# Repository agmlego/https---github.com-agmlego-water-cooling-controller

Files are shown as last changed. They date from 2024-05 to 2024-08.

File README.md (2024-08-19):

External Water-Cooling Loop Controller
--------------------------------------

The intent of this project is to monitor and control an external chiller system for a PC water-cooling loop with a liquid-liquid heat exchanger to separate the internal and external loops.

There is a PCIe x1 card inside the PC, tapping into SMBus and +3V3AUX, to monitor the flow, inlet, and outlet temperatures for the internal and external loops, and intercept the front panel power switch to prevent boot or to initiate a shutdown if the loops are not working correctly. The Teensy 3.2 will communicate to the PC, pretending to be a common SMBus device such as those from Winbond or Nuvoton. It also talks with an external board in the chiller over RS232. Onboard WS2811B and an OLED screen show immediate diagnostics. An onboard BME280 lets the Teensy monitor internal case ambient temperature and humidity, to ensure that the chiller does not drop below the local dewpoint to prevent condensation.

The external board listens to RS232 and adjusts the chiller's power state and setpoint. It also reports the local BME280 results and has an onboard OLED screen for system status.

## Internal PCIe Card

| Pin | Type | Signal | Direction | Purpose |
| --- | --- | --- | --- | --- |
| 1 | POWER | GND | | Digital ground plane |
| 2 | DIGITAL | D0 | INPUT | Internal loop flow sensor |
| 3 | DIGITAL | D1 | INPUT | External loop flow sensor |
| 7 | DIGITAL | D5 | OUTPUT | Level shifter output enable, active low |
| 8 | DIGITAL | D6 | INPUT | PCIe #PERST status |
| 9 | DIGITAL | D7 | OUTPUT | WS2811B data |
| 11  | RS232 | RX | INPUT | RS232 receive |
| 12  | RS232 | TX | OUTPUT | RS232 transmit |
| 21  | ANALOG  | A0 | INPUT | External loop outflow temperature, 10k NTC |
| 22  | ANALOG  | A1 | INPUT | External loop inflow temperature, 10k NTC |
| 23  | ANALOG  | A2 | INPUT | Internal loop inflow temperature, 10k NTC  |
| 24  | ANALOG  | A3 | INPUT | Internal loop outflow temperature, 10k NTC |
| 25  | I2C | SDA0 | BIDI | SMBus I2C data |
| 26  | I2C | SCL0 | BIDI | SMBus I2C clock |
| 29  | DIGITAL | D22 | OUTPUT | Front panel power switch output |
| 30  | DIGITAL | D23 | INPUT | Front panel power switch input |
| 31  | POWER | 3V3 | | 3.3V AUX input |
| 32  | POWER | AGND | | Analog ground plane |
| 42  | POWER | 3V3 | | 3.3V AUX input |
| 46  | I2C | SDA1 | BIDI | Local I2C data |
| 47  | I2C | SCL1 | BIDI | Local I2C clock |
| 53  | POWER | GND | | Digital ground plane |

### WS2811B

1. External loop temperature status
2. External loop flow status
3. Internal loop temperature status
4. Internal loop flow status

### RS232 DE-9

0. Chassis earth
1. N/C
2. PC RX
3. PC TX
4. N/C
5. 0VDC
6. N/C
7. N/C
8. N/C
9. +5V

### Images
top
bottom
[Interactive BOM](https://agmlego.github.io/water-cooling-controller/pcie/ibom.html)

## Chiller Controller

| Pin | Type | Signal | Direction | Purpose |
| --- | --- | --- | --- | --- |
| 1 | POWER | GND | | Digital ground |
| 2 | RS232 | RX | INPUT | RS232 receive |
| 3 | RS232 | TX | OUTPUT | RS232 transmit |
| 4 | 1-WIRE  | D2 | BIDI | DS18B20 bus |
| 10  | DIGITAL | D8 | OUTPUT | Expansion valve relay |
| 11  | DIGITAL | D9 | OUTPUT | Compressor relay |
| 12  | DIGITAL | D10 | OUTPUT | [Fan PWM](#nf-a14-control) |
| 13  | DIGITAL | D11 | INPUT | Bottom fan RPM sensor |
| 14  | DIGITAL | D12 | INPUT | Top fan RPM sensor |
| 20  | DIGITAL | D13 | OUTPUT | Status lights/buzzer relay |
| 21  | DIGITAL | D14 | OUTPUT | Pump relay |
| 22  | DIGITAL | D15 | INPUT | Flow switch, active low |
| 23  | I2C | SCL0 | BIDI | Local I2C clock |
| 24  | I2C | SDA0 | BIDI | Local I2C data |
| 25  | DIGITAL | D18 | INPUT | Encoder switch |
| 26  | DIGITAL | D19 | INPUT | Encoder quadrature B |
| 27  | DIGITAL | D20 | INPUT | Encoder quadrature A |
| 28  | ANALOG  | A7 | INPUT | Filter check diff. pressure sensor |
| 29  | ANALOG  | A8 | INPUT | Reservoir eTape R<sub>ref</sub> 2000Ω |
| 30  | ANALOG  | A9 | INPUT | Reservoir eTape R<sub>sense</sub> 400-2000Ω |
| 31  | POWER | 3V3 | | 3.3V output |
| 32  | POWER | AGND | | Analog ground |
| 33  | POWER | 5V | | 5V input from CAN |

### JST-XH Connectors

#### RS232
| Pin | Type  | Signal | Direction | Purpose |
| --- | ----- | --- | --- | --- |
| 1 | POWER | 5V | | 5V from PCIe card |
| 2 | POWER | GND | | Digital ground |
| 3 | RS232 | RX | INPUT | RS232 receive |
| 4 | RS232 | TX | OUTPUT | RS232 transmit |

#### Flow
| Pin | Type | Signal | Direction | Purpose |
| --- | --- | --- | --- | --- |
| 1 | DIGITAL | D15 | INPUT | Flow switch |
| 2 | POWER | GND | | Digital ground |

#### DS18B20 One-Wire
| Pin | Type | Signal | Direction | Purpose |
| --- | --- | --- | --- | --- |
| 1 | 1-WIRE | D2 | BIDI | DS18B20 bus |
| 2 | POWER  | GND | | Digital ground |
| 3 | POWER  | 3V3 | | 3.3V output |

#### Filter Diff. Pressure
| Pin | Type | Signal | Direction | Purpose |
| --- | --- | --- | --- | --- |
| 1 | POWER  | 3V3 | | 3.3V output |
| 2 | POWER  | AGND | | Analog ground |
| 3 | ANALOG | A7 | INPUT | Filter check diff. pressure sensor |

#### Reservoir Level eTape
| Pin | Type | Signal | Direction | Purpose |
| --- | --- | --- | --- | --- |
| 1 | ANALOG | A9 | INPUT | R<sub>sense</sub> 400-2000Ω |
| 2 | ANALOG | A8 | INPUT | R<sub>ref</sub> 2000Ω |
| 3 | POWER  | AGND | | Analog ground |
| 4 | POWER  | AGND | | Analog ground |

#### Fans
| Pin | Type | Signal | Direction | Purpose |
| --- | --- | --- | --- | --- |
| 1 | DIGITAL | D12 | INPUT | Top fan RPM sensor |
| 2 | DIGITAL | D11 | INPUT | Bottom fan RPM sensor |
| 3 | DIGITAL | D10 | OUTPUT | Fan PWM |

#### Dual-Relay Module
| Pin | Type | Signal | Direction | Purpose |
| --- | --- | --- | --- | --- |
| 1 | POWER | GND | | Digital ground |
| 2 | DIGITAL | D13 | OUTPUT | Status lights/buzzer relay |
| 3 | DIGITAL | D14 | OUTPUT | Pump relay |
| 4 | POWER | 5V | | 5V input from CAN |

#### SSRs
| Pin | Type | Signal | Direction | Purpose |
| --- | --- | --- | --- | --- |
| 1 | POWER | GND | | Digital ground |
| 2 | DIGITAL | D9 | OUTPUT | Compressor relay |
| 3 | POWER | GND | | Digital ground |
| 4 | DIGITAL | D8 | OUTPUT | Expansion valve relay |

### NF-A14 Control
* PWM: 40μs period, 5Vpp
* 8.76% minimum kickon => 468RPM (64ms/15.6Hz on tach.)
* 100% => 3180RPM (9.4ms/106.4Hz on tach.)

### Images
top
bottom
[Interactive BOM](https://agmlego.github.io/water-cooling-controller/cw5200/ibom.html)

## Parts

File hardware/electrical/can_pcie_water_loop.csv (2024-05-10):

Source: | D:\documents\projects\home_automation\can_pcie_water_loop\can_pcie_water_loop.kicad_sch
Date: | 2023-08-21 20:34:38
Tool: | Eeschema (7.0.0)
Generator: | C:\Program Files\KiCad\7.0\bin\scripting\plugins/bom_csv_grouped_by_value_with_fp.py
Component Count: | 56
Ref | Qnty | Value | Cmp name | Footprint | Description | Vendor | DNP
C1 | 1 | 4700pF | C_Small | Capacitor_SMD:C_1206_3216Metric | Unpolarized capacitor, small symbol
C2, C3 | 2 | 0.1uF | C_Small | Capacitor_SMD:C_1206_3216Metric | Unpolarized capacitor, small symbol
D1, D2, D3, D4, D5, D6 | 6 | GREEN | LED_Small | LED_SMD:LED_1206_3216Metric | Light emitting diode, small symbol
D7 | 1 | Ext T Stat | WS2812B | LED_SMD:LED_WS2812B_PLCC4_5.0x5.0mm_P3.2mm | RGB LED with integrated controller
D8 | 1 | Ext Flo Stat | WS2812B | LED_SMD:LED_WS2812B_PLCC4_5.0x5.0mm_P3.2mm | RGB LED with integrated controller
D9 | 1 | Int T Stat | WS2812B | LED_SMD:LED_WS2812B_PLCC4_5.0x5.0mm_P3.2mm | RGB LED with integrated controller
D10 | 1 | Int Flo Stat | WS2812B | LED_SMD:LED_WS2812B_PLCC4_5.0x5.0mm_P3.2mm | RGB LED with integrated controller
H1, H2 | 2 | PCIe Bracket | MountingHole_Pad | MountingHole:MountingHole_3.2mm_M3_Pad_Via | Mounting Hole with connection
H3, H4, H5, H6 | 4 | OLED | MountingHole | MountingHole:MountingHole_2.2mm_M2 | Mounting Hole without connection
H7 | 1 | BME280 | MountingHole | MountingHole:MountingHole_3.2mm_M3 | Mounting Hole without connection
J1 | 1 | Bus_PCI_Express_x1 | Bus_PCI_Express_x1 | Connector_PCBEdge:BUS_PCIexpress_x1 | PCI Express bus connector x1
J2 | 1 | CAN | DE9_Plug_MountingHoles | Connector_Dsub:DSUB-9_Female_Horizontal_P2.77x2.84mm_EdgePinOffset7.70mm_Housed_MountingHolesOffset9.12mm | 9-pin male plug pin D-SUB connector, Mounting Hole
J3 | 1 | Int T Hi | Conn_01x02_Pin | Connector_PinHeader_2.54mm:PinHeader_1x02_P2.54mm_Horizontal | Generic connector, single row, 01x02, script generated
J4 | 1 | Int T Lo | Conn_01x02_Pin | Connector_PinHeader_2.54mm:PinHeader_1x02_P2.54mm_Horizontal | Generic connector, single row, 01x02, script generated
J5 | 1 | Ext T Hi | Conn_01x02_Pin | Connector_PinHeader_2.54mm:PinHeader_1x02_P2.54mm_Horizontal | Generic connector, single row, 01x02, script generated
J6 | 1 | Ext T Lo | Conn_01x02_Pin | Connector_PinHeader_2.54mm:PinHeader_1x02_P2.54mm_Horizontal | Generic connector, single row, 01x02, script generated
J7 | 1 | BME280 I2C | Conn_01x04_Pin | Connector_PinHeader_2.54mm:PinHeader_1x04_P2.54mm_Vertical | Generic connector, single row, 01x04, script generated
J8 | 1 | Disp I2C | Conn_01x04_Pin | Connector_PinHeader_2.54mm:PinHeader_1x04_P2.54mm_Vertical | Generic connector, single row, 01x04, script generated
J9 | 1 | Int Flo | Conn_01x03_Pin | Connector_PinHeader_2.54mm:PinHeader_1x03_P2.54mm_Horizontal | Generic connector, single row, 01x03, script generated
J10 | 1 | Ext Flo | Conn_01x03_Pin | Connector_PinHeader_2.54mm:PinHeader_1x03_P2.54mm_Horizontal | Generic connector, single row, 01x03, script generated
J11 | 1 | SW In | Conn_01x02_Pin | Connector_PinHeader_2.54mm:PinHeader_1x02_P2.54mm_Horizontal | Generic connector, single row, 01x02, script generated
J12 | 1 | SW Out | Conn_01x02_Pin | Connector_PinHeader_2.54mm:PinHeader_1x02_P2.54mm_Horizontal | Generic connector, single row, 01x02, script generated
J13 | 1 | SMBus | Conn_01x04_Pin | Connector_PinHeader_2.54mm:PinHeader_1x04_P2.54mm_Vertical | Generic connector, single row, 01x04, script generated
R1, R7, R8, R17, R18 | 5 | 10k | R_Small_US | Resistor_SMD:R_1206_3216Metric | Resistor, small US symbol
R2 | 1 | 200 | R_Small_US | Resistor_SMD:R_1206_3216Metric | Resistor, small US symbol
R3, R4, R5, R6 | 4 | 100k | R_Small_US | Resistor_SMD:R_1206_3216Metric | Resistor, small US symbol
R9, R10 | 2 | 60 | R_Small_US | Resistor_SMD:R_1206_3216Metric | Resistor, small US symbol
R11 | 1 | 300 | R_Small_US | Resistor_SMD:R_1206_3216Metric | Resistor, small US symbol
R12, R13, R14, R15, R16 | 5 | 220 | R_Small_US | Resistor_SMD:R_1206_3216Metric | Resistor, small US symbol
U1 | 1 | Teensy3.2 | Teensy3.2 | teensy:Teensy30_31_32_All_Pins
U2 | 1 | MCP2561 | MCP2561-E-SN | Package_SO:SOIC-8_3.9x4.9mm_P1.27mm | High-Speed CAN Transceiver, 1Mbps, 5V supply, SPLIT pin, -40C to +125C, SOIC-8
U3 | 1 | CNY17-3 | CNY17-3 | Package_DIP:SMDIP-6_W7.62mm | DC Optocoupler Base Connected, Vce 70V, CTR 100-200%, Viso 5000V (RMS), DIP6
U4 | 1 | Pololu U3V16F5 | TSR_1-2412 | Connector_PinHeader_2.54mm:PinHeader_1x03_P2.54mm_Vertical | 1A step-down regulator module, fixed 1.2V output voltage, 6-36V input voltage, -40°C to +85°C temperature range, TO-220 compatible LM78xx replacement
U5 | 1 | 74125 | SN74LV4T125 | Package_SO:TSSOP-14_4.4x5mm_P0.65mm | Single Supply Logic Level Translator Quad Buffer with 3-State Outputs

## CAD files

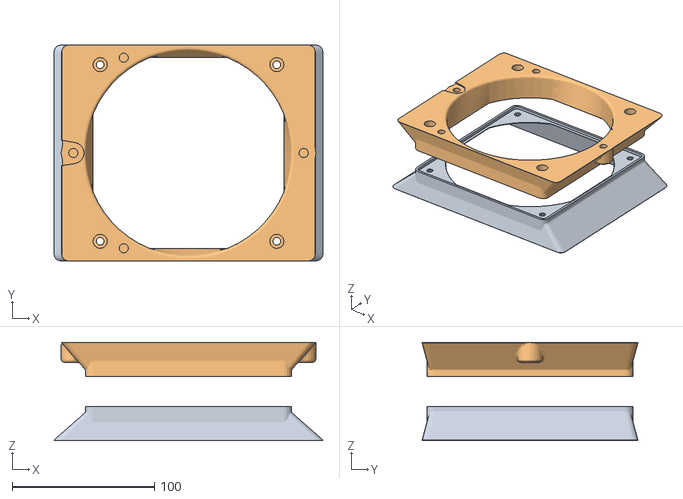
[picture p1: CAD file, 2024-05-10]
hardware/mechanical/nf-a14_ducting.obj
189.2 x 151.8 x 69.0
coil_side
exhaust_side

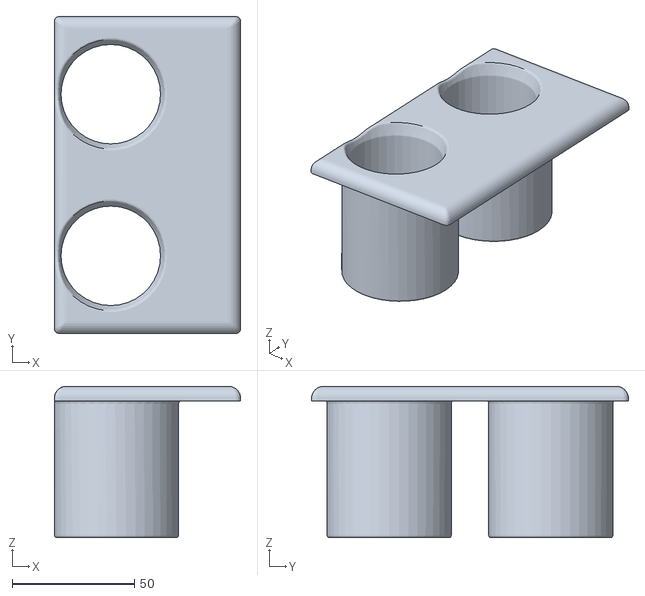
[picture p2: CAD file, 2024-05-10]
hardware/mechanical/wall_passthrough.obj
76.2 x 129.5 x 61.9

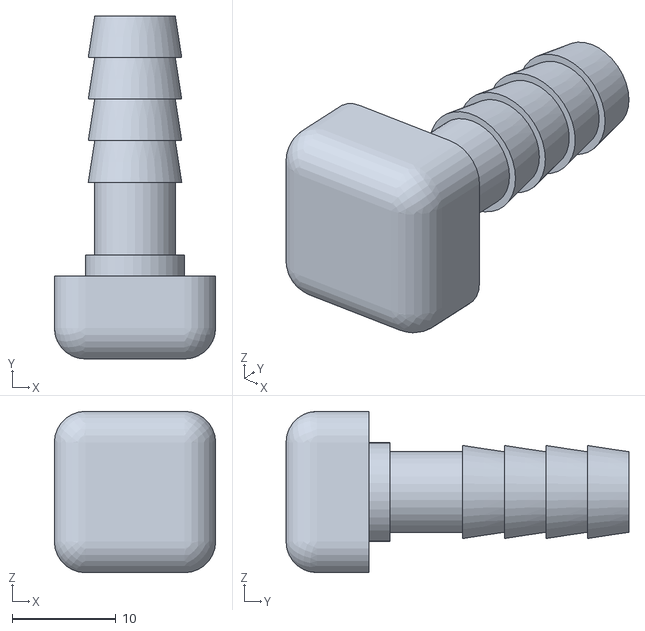
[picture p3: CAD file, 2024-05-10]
hardware/mechanical/vacuum_vent.obj
15.5 x 33.0 x 15.5

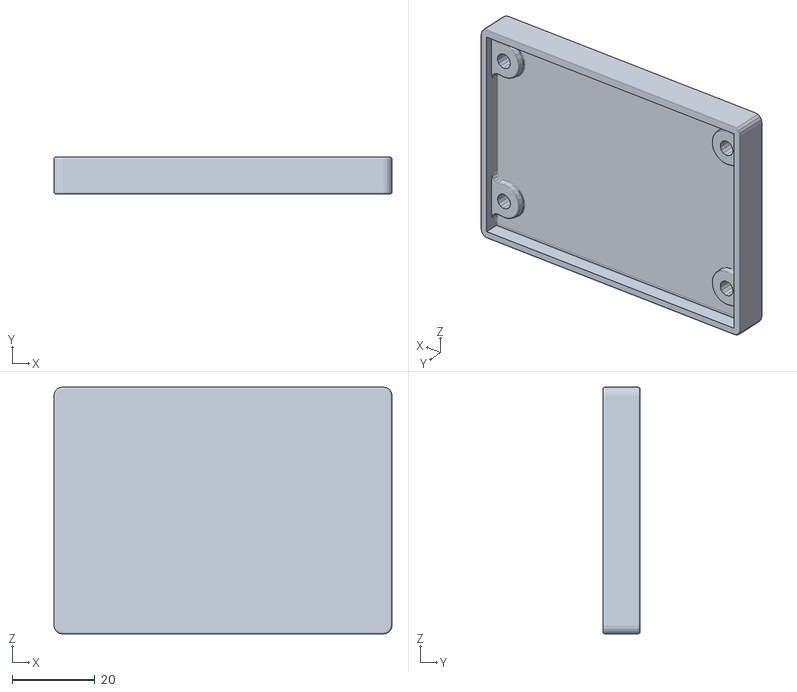
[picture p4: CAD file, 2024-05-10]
hardware/mechanical/vma400_isolator.obj
81.5 x 9.00 x 59.5

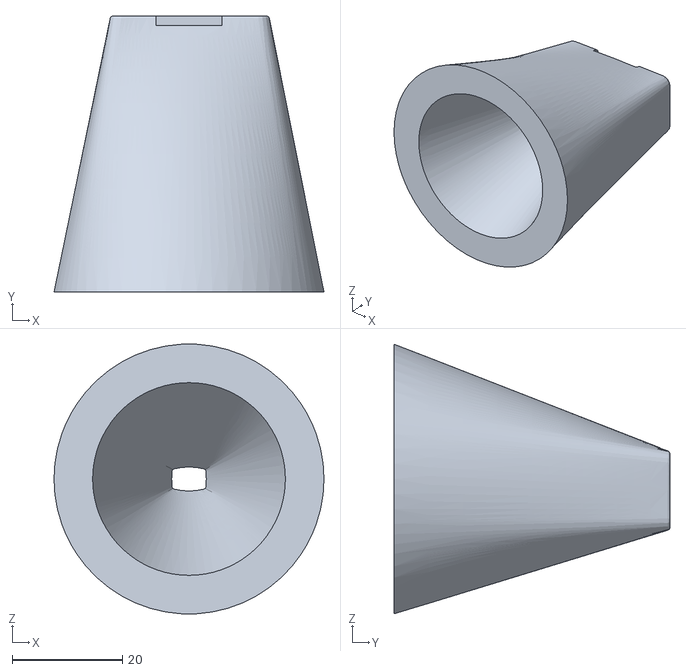
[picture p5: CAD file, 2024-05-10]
hardware/mechanical/VL53L0X_standoff.obj
48.9 x 50.0 x 48.8

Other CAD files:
hardware/mechanical/VL53L0X_standoff.ipt
hardware/mechanical/nf-a14.ipt
hardware/mechanical/nf-a14_ducting.ipt
hardware/mechanical/vacuum_vent.ipt
hardware/mechanical/vma400_isolator.ipt
hardware/mechanical/wall_passthrough.ipt

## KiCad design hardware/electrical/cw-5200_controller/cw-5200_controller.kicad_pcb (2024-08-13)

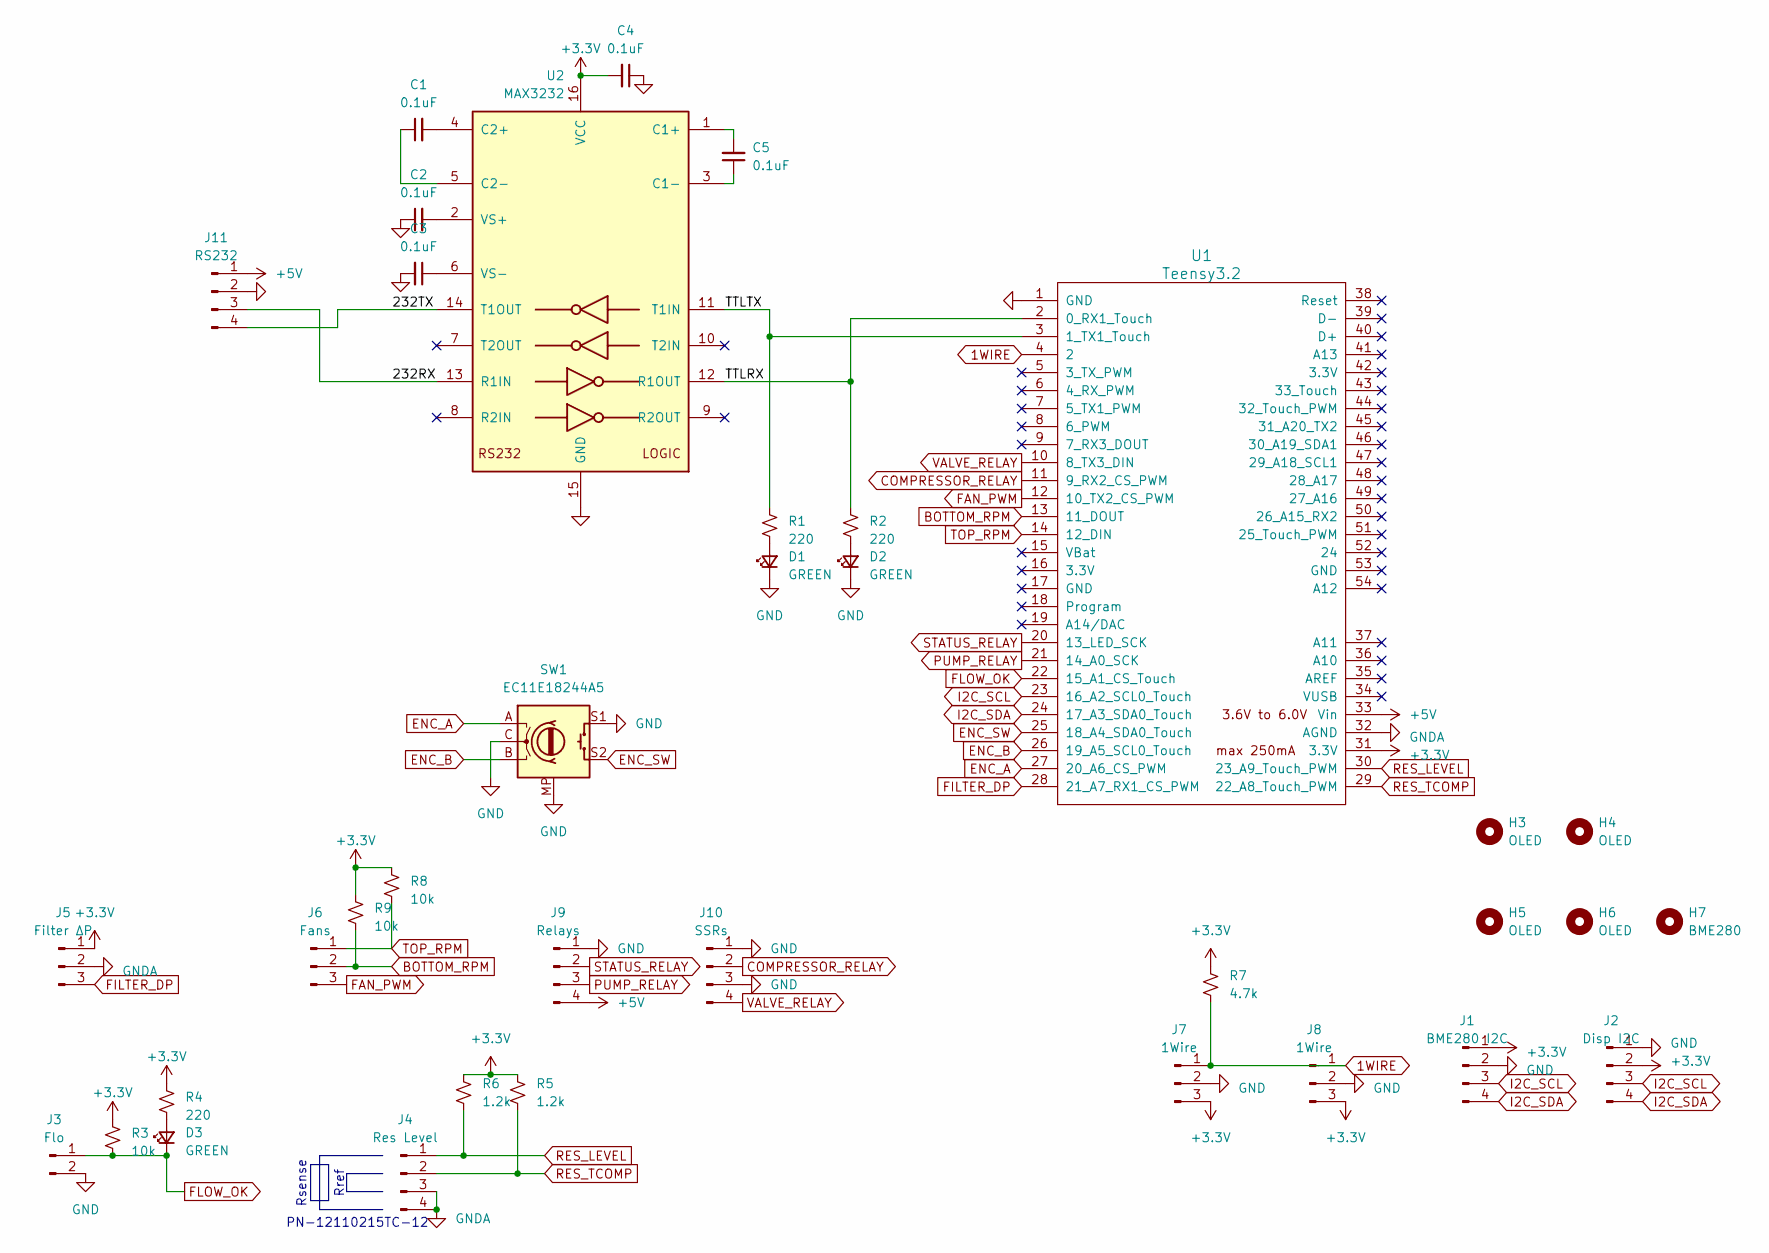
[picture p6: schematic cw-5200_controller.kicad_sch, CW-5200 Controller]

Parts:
C1, C2, C3, C4, C5: 0.1uF; C_1206_3216Metric
D1, D2, D3: GREEN; LED_1206_3216Metric
H3, H4, H5, H6: OLED; MountingHole_2.2mm_M2
H7: BME280; MountingHole_3.2mm_M3
J1: BME280 I2C; PinHeader_1x04_P2.54mm_Vertical
J2: Disp I2C; PinHeader_1x04_P2.54mm_Vertical
J3: Flo; JST_XH_B2B-XH-A_1x02_P2.50mm_Vertical
J4: Res Level; JST_XH_B4B-XH-A_1x04_P2.50mm_Vertical
J5: Filter ΔP; JST_XH_B3B-XH-A_1x03_P2.50mm_Vertical
J6: Fans; JST_XH_B3B-XH-A_1x03_P2.50mm_Vertical
J7, J8: 1Wire; JST_XH_B3B-XH-A_1x03_P2.50mm_Vertical
J9: Relays; JST_XH_B4B-XH-A_1x04_P2.50mm_Vertical
J10: SSRs; JST_XH_B4B-XH-A_1x04_P2.50mm_Vertical
J11: RS232; JST_XH_B4B-XH-A_1x04_P2.50mm_Vertical
R1, R2, R4: 220; R_1206_3216Metric
R3, R8, R9: 10k; R_1206_3216Metric
R5, R6: 1.2k; R_1206_3216Metric
R7: 4.7k; R_1206_3216Metric
SW1: EC11E18244A5; RotaryEncoder_Alps_EC11E-Switch_Vertical_H20mm
U1: Teensy3.2; Teensy30_31_32_All_Pins
U2: MAX3232; TSSOP-16_4.4x5mm_P0.65mm

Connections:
1WIRE: J7.1, J8.1, R7.1, U1.4 (2)
+3.3V: C4.2, J1.1, J2.2, J5.1, J7.3, J8.3, R3.1, R4.1, R5.2, R6.1, R7.2, R8.1, R9.1, U1.31 (3.3V), U2.16 (VCC)
+5V: J9.4, J11.1, U1.33 (Vin)
/232RX: J11.3, U2.13 (R1IN)
/232TX: J11.4, U2.14 (T1OUT)
/TTLRX: R2.1, U1.2 (0_RX1_Touch), U2.12 (R1OUT)
/TTLTX: R1.1, U1.3 (1_TX1_Touch), U2.11 (T1IN)
BOTTOM_RPM: J6.2, R9.2, U1.13 (11_DOUT)
COMPRESSOR_RELAY: J10.2, U1.11 (9_RX2_CS_PWM)
ENC_A: SW1.A, U1.27 (20_A6_CS_PWM)
ENC_B: SW1.B, U1.26 (19_A5_SCL0_Touch)
ENC_SW: SW1.S2, U1.25 (18_A4_SDA0_Touch)
FAN_PWM: J6.3, U1.12 (10_TX2_CS_PWM)
FILTER_DP: J5.3, U1.28 (21_A7_RX1_CS_PWM)
FLOW_OK: D3.1 (K), J3.1, R3.2, U1.22 (15_A1_CS_Touch)
GND: C2.1, C3.2, C4.1, D1.1 (K), D2.1 (K), J1.2, J2.1, J3.2, J7.2, J8.2, J9.1, J10.1, J10.3, J11.2, SW1.C, SW1.MP, SW1.S1, U1.1 (GND), U2.15 (GND)
GNDA: J4.3, J4.4, J5.2, U1.32 (AGND)
I2C_SCL: J1.3, J2.3, U1.23 (16_A2_SCL0_Touch)
I2C_SDA: J1.4, J2.4, U1.24 (17_A3_SDA0_Touch)
unnamed: D1.2 (A), R1.2
unnamed: D2.2 (A), R2.2
unnamed: D3.2 (A), R4.2
unnamed: C5.2, U2.1 (C1+)
unnamed: C5.1, U2.3 (C1-)
unnamed: C1.2, U2.4 (C2+)
unnamed: C1.1, U2.5 (C2-)
unnamed: C2.2, U2.2 (VS+)
unnamed: C3.1, U2.6 (VS-)
PUMP_RELAY: J9.3, U1.21 (14_A0_SCK)
RES_LEVEL: J4.1, R6.2, U1.30 (23_A9_Touch_PWM)
RES_TCOMP: J4.2, R5.1, U1.29 (22_A8_Touch_PWM)
STATUS_RELAY: J9.2, U1.20 (13_LED_SCK)
TOP_RPM: J6.1, R8.2, U1.14 (12_DIN)
VALVE_RELAY: J10.4, U1.10 (8_TX3_DIN)

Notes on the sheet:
PN-12110215TC-12
Rref
Rsense

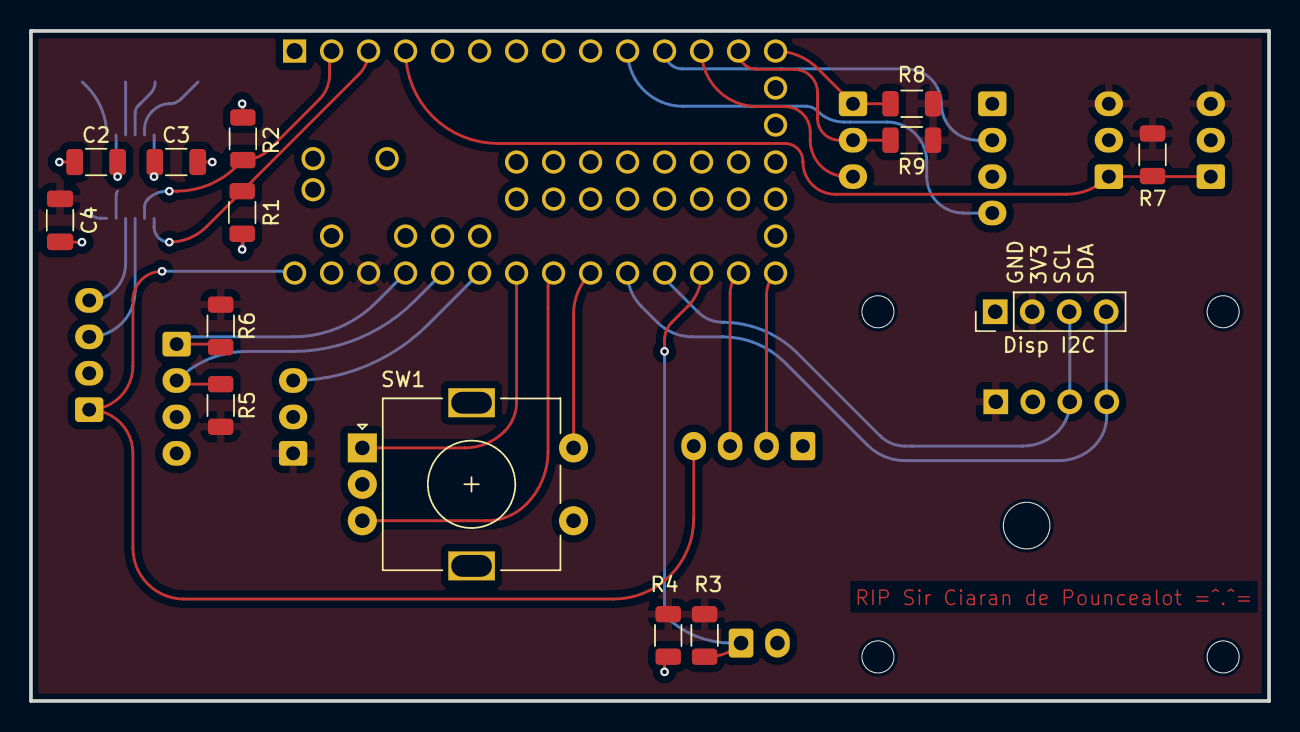
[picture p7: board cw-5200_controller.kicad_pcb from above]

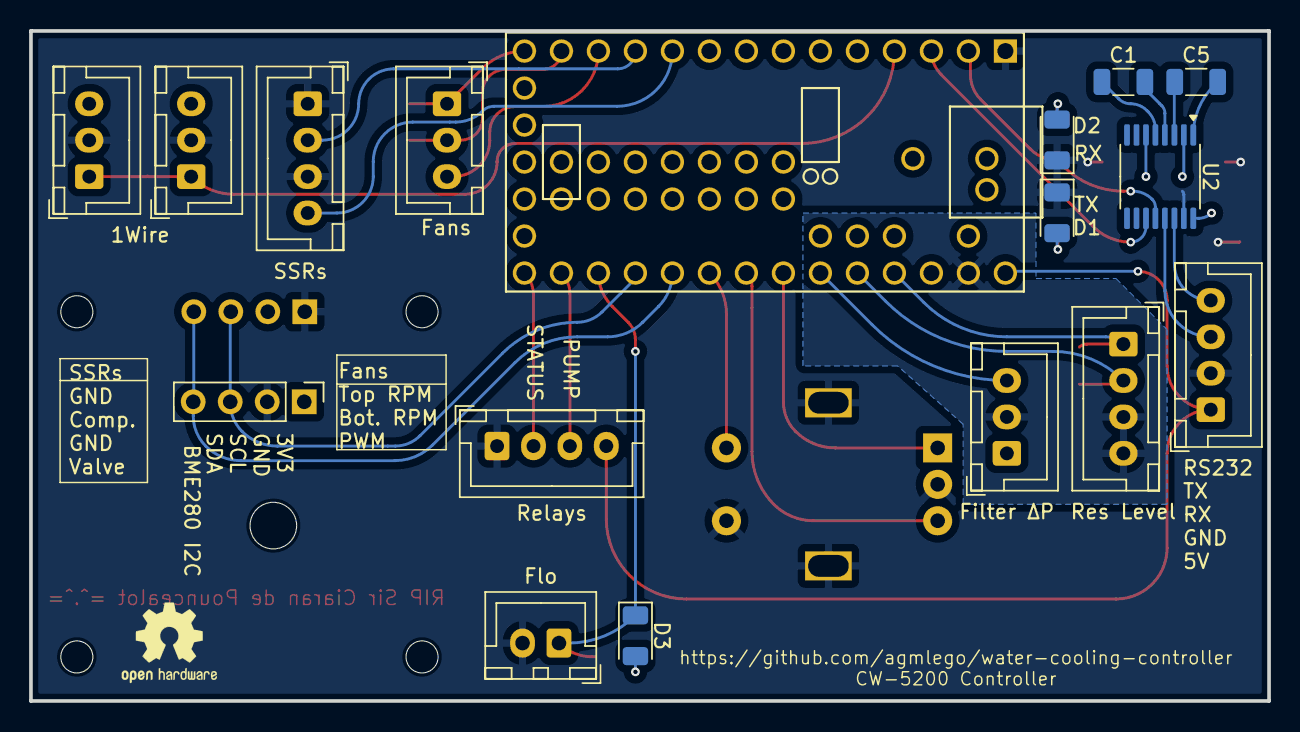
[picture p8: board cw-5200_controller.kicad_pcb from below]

Board: 2 copper layers, 85.0 x 46.0 mm, 36 parts (17 on the bottom side), 34 nets.

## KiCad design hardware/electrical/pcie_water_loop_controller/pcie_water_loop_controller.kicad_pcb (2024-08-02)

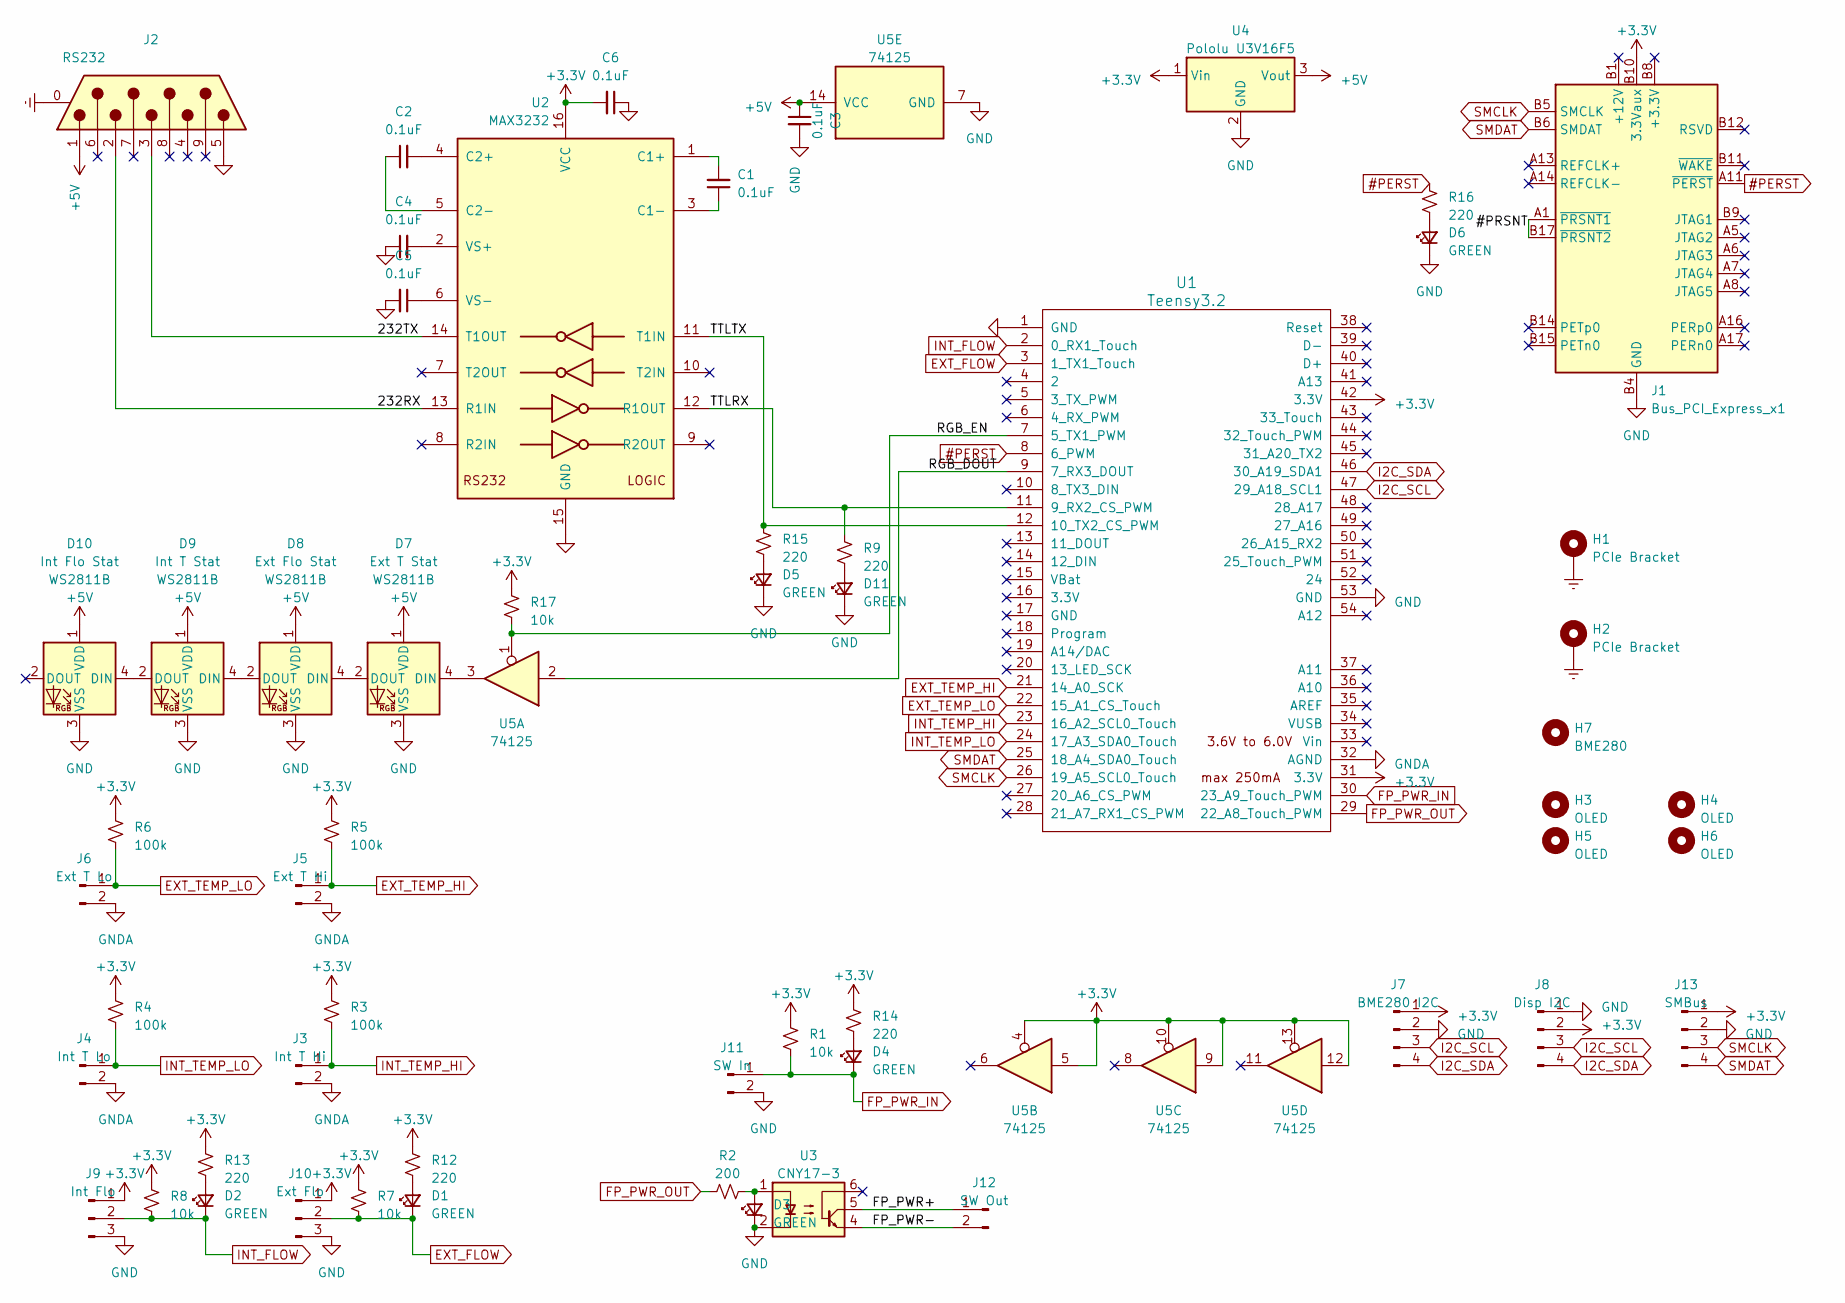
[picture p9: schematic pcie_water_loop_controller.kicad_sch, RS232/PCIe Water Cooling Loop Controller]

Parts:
C1, C2, C3, C4, C5, C6: 0.1uF; C_1206_3216Metric
D1, D2, D3, D4, D5, D6, D11: GREEN; LED_1206_3216Metric
D7: Ext T Stat; LED_WS2812B_PLCC4_5.0x5.0mm_P3.2mm
D8: Ext Flo Stat; LED_WS2812B_PLCC4_5.0x5.0mm_P3.2mm
D9: Int T Stat; LED_WS2812B_PLCC4_5.0x5.0mm_P3.2mm
D10: Int Flo Stat; LED_WS2812B_PLCC4_5.0x5.0mm_P3.2mm
H1, H2: PCIe Bracket; MountingHole_3.2mm_M3_Pad_Via
H3, H4, H5, H6: OLED; MountingHole_2.2mm_M2
H7: BME280; MountingHole_3.2mm_M3
J1: Bus_PCI_Express_x1; BUS_PCIexpress_x1
J2: RS232; DSUB-9_Female_Horizontal_P2.77x2.84mm_EdgePinOffset7.70mm_H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
J3: Int T Hi; PinHeader_1x02_P2.54mm_Horizontal
J4: Int T Lo; PinHeader_1x02_P2.54mm_Horizontal
J5: Ext T Hi; PinHeader_1x02_P2.54mm_Horizontal
J6: Ext T Lo; PinHeader_1x02_P2.54mm_Horizontal
J7: BME280 I2C; PinHeader_1x04_P2.54mm_Vertical
J8: Disp I2C; PinHeader_1x04_P2.54mm_Vertical
J9: Int Flo; PinHeader_1x03_P2.54mm_Horizontal
J10: Ext Flo; PinHeader_1x03_P2.54mm_Horizontal
J11: SW In; PinHeader_1x02_P2.54mm_Horizontal
J12: SW Out; PinHeader_1x02_P2.54mm_Horizontal
J13: SMBus; PinHeader_1x04_P2.54mm_Vertical
R1, R7, R8, R17: 10k; R_1206_3216Metric
R2: 200; R_1206_3216Metric
R3, R4, R5, R6: 100k; R_1206_3216Metric
R9, R12, R13, R14, R15, R16: 220; R_1206_3216Metric
U1: Teensy3.2; Teensy30_31_32_All_Pins
U2: MAX3232; TSSOP-16_4.4x5mm_P0.65mm
U3: CNY17-3; SMDIP-6_W7.62mm
U4: Pololu U3V16F5; PinHeader_1x03_P2.54mm_Vertical
U5: 74125; TSSOP-14_4.4x5mm_P0.65mm

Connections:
#PERST: J1.A11 (~PERST), R16.1, U1.8 (6_PWM)
+3.3V: C6.2, J1.B10 (3.3Vaux), J7.1, J8.2, J9.1, J10.1, J13.1, R1.1, R3.1, R4.1, R5.1, R6.1, R7.1, R8.1, R12.1, R13.1, R14.1, R17.1, U1.31 (3.3V), U1.42 (3.3V), U2.16 (VCC), U4.1 (Vin), U5.4, U5.5, U5.9, U5.10, U5.12, U5.13
+5V: C3.1, D7.1 (VDD), D8.1 (VDD), D9.1 (VDD), D10.1 (VDD), J2.1, U4.3 (Vout), U5.14 (VCC)
/232RX: J2.2, U2.13 (R1IN)
/232TX: J2.3, U2.14 (T1OUT)
/#PRSNT: J1.A1 (~PRSNT1), J1.B17 (~PRSNT2)
/FP_PWR+: J12.1, U3.5
/FP_PWR-: J12.2, U3.4
/RGB_DOUT: U1.9 (7_RX3_DOUT), U5.2
/RGB_EN: R17.2, U1.7 (5_TX1_PWM), U5.1
/TTLRX: R9.1, U1.11 (9_RX2_CS_PWM), U2.12 (R1OUT)
/TTLTX: R15.1, U1.12 (10_TX2_CS_PWM), U2.11 (T1IN)
EXT_FLOW: D1.1 (K), J10.2, R7.2, U1.3 (1_TX1_Touch)
EXT_TEMP_HI: J5.1, R5.2, U1.21 (14_A0_SCK)
EXT_TEMP_LO: J6.1, R6.2, U1.22 (15_A1_CS_Touch)
Earth: H1.1, H2.1, J2.0 (PAD)
FP_PWR_IN: D4.1 (K), J11.1, R1.2, U1.30 (23_A9_Touch_PWM)
FP_PWR_OUT: R2.2, U1.29 (22_A8_Touch_PWM)
GND: C3.2, C4.1, C5.2, C6.1, D3.1 (K), D5.1 (K), D6.1 (K), D7.3 (VSS), D8.3 (VSS), D9.3 (VSS), D10.3 (VSS), D11.1 (K), J1.A4 (GND), J1.A12 (GND), J1.A15 (GND), J1.A18 (GND), J1.B4 (GND), J1.B7 (GND), J1.B13 (GND), J1.B16 (GND), J1.B18 (GND), J2.5, J7.2, J8.1, J9.3, J10.3, J11.2, J13.2, U1.1 (GND), U1.53 (GND), U2.15 (GND), U3.2, U4.2 (GND), U5.7 (GND)
GNDA: J3.2, J4.2, J5.2, J6.2, U1.32 (AGND)
I2C_SCL: J7.3, J8.3, U1.47 (29_A18_SCL1)
I2C_SDA: J7.4, J8.4, U1.46 (30_A19_SDA1)
INT_FLOW: D2.1 (K), J9.2, R8.2, U1.2 (0_RX1_Touch)
INT_TEMP_HI: J3.1, R3.2, U1.23 (16_A2_SCL0_Touch)
INT_TEMP_LO: J4.1, R4.2, U1.24 (17_A3_SDA0_Touch)
unnamed: D1.2 (A), R12.2
unnamed: D2.2 (A), R13.2
unnamed: D3.2 (A), R2.1, U3.1
unnamed: D4.2 (A), R14.2
unnamed: D5.2 (A), R15.2
unnamed: D6.2 (A), R16.2
unnamed: D7.4 (DIN), U5.3
unnamed: D7.2 (DOUT), D8.4 (DIN)
unnamed: D8.2 (DOUT), D9.4 (DIN)
unnamed: D9.2 (DOUT), D10.4 (DIN)
unnamed: D11.2 (A), R9.2
unnamed: C1.2, U2.1 (C1+)
unnamed: C1.1, U2.3 (C1-)
unnamed: C2.2, U2.4 (C2+)
unnamed: C2.1, U2.5 (C2-)
unnamed: C4.2, U2.2 (VS+)
unnamed: C5.1, U2.6 (VS-)
SMCLK: J1.B5 (SMCLK), J13.3, U1.26 (19_A5_SCL0_Touch)
SMDAT: J1.B6 (SMDAT), J13.4, U1.25 (18_A4_SDA0_Touch)

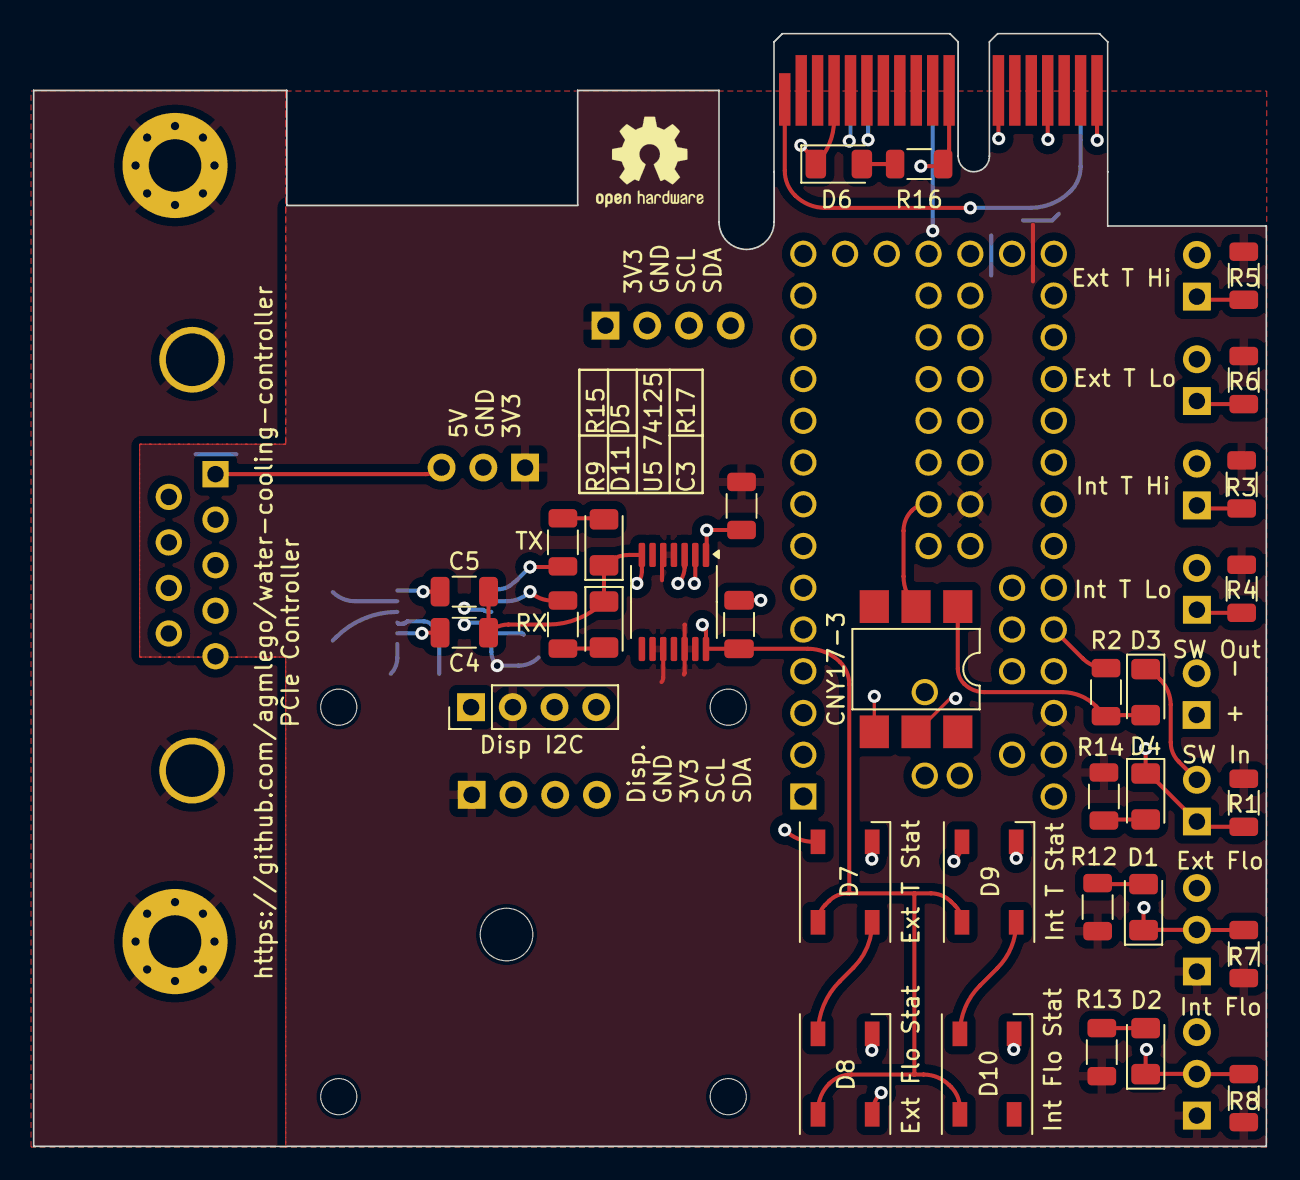
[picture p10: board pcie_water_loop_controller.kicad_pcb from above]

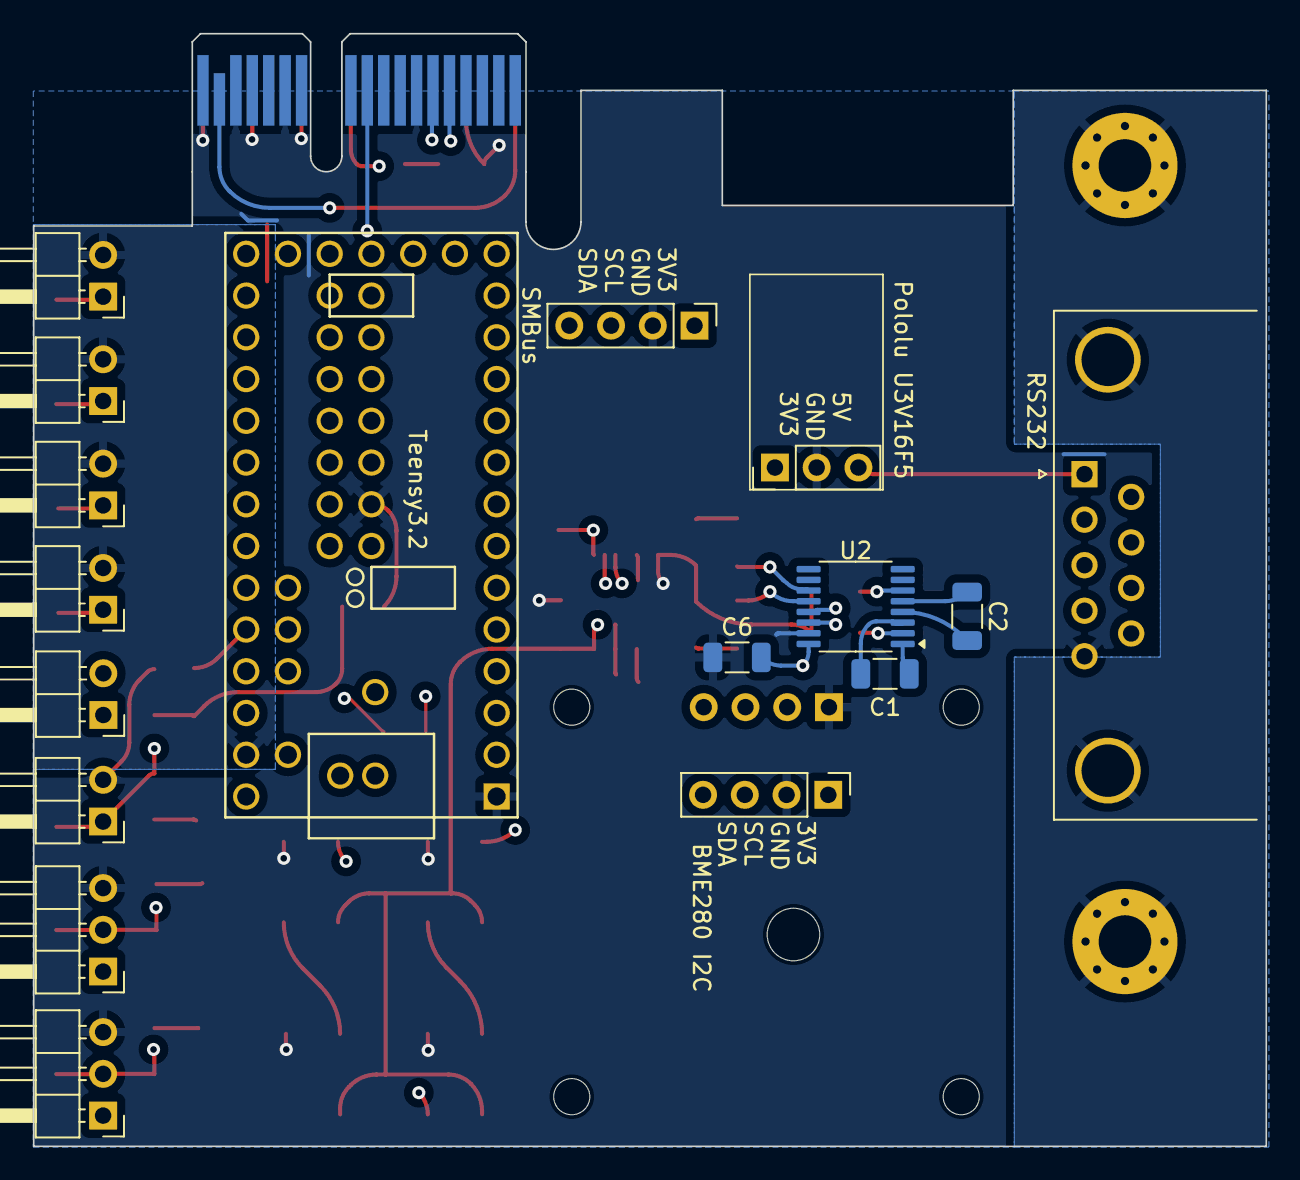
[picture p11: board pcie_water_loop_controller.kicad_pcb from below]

Board: 4 copper layers, 75.0 x 67.7 mm, 57 parts (18 on the bottom side), 44 nets.

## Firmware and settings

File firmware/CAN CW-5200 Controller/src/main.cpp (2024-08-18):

#include <Arduino.h>
#include <FreqMeasureMulti.h>
#include <Adafruit_BME280.h>
#include <Adafruit_GFX.h>
#include <Adafruit_SSD1306.h>
#include <RunningAverage.h>
#include <OneWire.h>
#include <DallasTemperature.h>
#include <SerialTransfer.h>

#include "error_codes.h"
#include "settings.h"
#include "comms.h"
#include "fans.h"

#define SER_RX 0          // Serial Rx
#define SER_TX 1          // Serial Tx
#define ONE_WIRE 2        // DS18B20 bus
#define VALVE_RLY 8       // OUTPUT valve
#define COMPRESSOR_RLY 9  // OUTPUT compressor
#define FAN_PWM 10        // OUTPUT fan PWM signal
#define BOTTOM_FAN_RPM 11 // INPUT Bottom fan tach
#define TOP_FAN_RPM 12    // INPUT Top fan tach
#define ALARMS_RLY 13     // OUTPUT alarms
#define PUMP_RLY 14       // OUTPUT pump
#define FLOW_SW 15        // INPUT PULLUP flow switch; low == OK
#define I2C_SDA 17        // Local I2C data
#define I2C_SCL 16        // Local I2C clock
#define ENCODER_SWITCH 18 // Encoder push switch
#define ENCODER_A 20      // Encoder quad channel A
#define ENCODER_B 19      // Encoder quad channel B
#define FILTER_P A7       // Analog input for differential pressure sensor
#define RES_LEVEL A9      // Analog input for eTape Rsense
#define RES_REF A8        // Analog input for eTape Rref

struct_readings readings;

RunningAverage filterRA(100);

#define FAN_SAMPLING_TIME 1000
volatile struct_fan top_fan;
volatile struct_fan bottom_fan;
RunningAverage topRA(10);
RunningAverage bottomRA(10);

#define BME_ADDRESS 0x76
Adafruit_BME280 bme; // use I2C interface
Adafruit_Sensor *bme_temp = bme.getTemperatureSensor();
Adafruit_Sensor *bme_humidity = bme.getHumiditySensor();

#define SCREEN_WIDTH 128 // OLED display width, in pixels
#define SCREEN_HEIGHT 64 // OLED display height, in pixels
#define FONT_X 5
#define FONT_Y 8
#define GAUGE_RADIUS 28
#define PAGE_DELAY 5000
#define OLED_RESET -1       // Reset pin # (or -1 if sharing Arduino reset pin)
#define SCREEN_ADDRESS 0x3C ///< See datasheet for Address; 0x3D for 128x64, 0x3C for 128x32
Adafruit_SSD1306 display(SCREEN_WIDTH, SCREEN_HEIGHT, &Wire, OLED_RESET);

RunningAverage resLvlRA(100);
RunningAverage resRefRA(100);

#define TEMPERATURE_PRECISION 9
OneWire oneWire(ONE_WIRE);
DallasTemperature sensors(&oneWire);
DeviceAddress outside_temp = {0x28, 0x4E, 0x6A, 0x45, 0x92, 0x17, 0x02, 0xEC};
DeviceAddress reservoir_temp = {0x28, 0xFF, 0x02, 0x5D, 0xC1, 0x17, 0x05, 0xCB};

uint32_t last_compressor = 0;
uint32_t last_valve = 0;

bool running_state = true;
uint32_t reading_time = 0;
uint8_t reading_state = 0;

struct_settings *settings;

SerialTransfer telemetry;
uint16_t txSize = 0;

void handleUSBSerial();
void measureReservoirLevel();
void measureChassisTempHumid();
void measureReservoirTemp();
void measureOutsideTemp();
void measureFanRPM();
void measureFilterDP();
void runCoolingCycle();
void setError(uint16_t);
void printAddress(DeviceAddress);
void updateDisplay();
void top_fan_pulse();
void bottom_fan_pulse();
int ringMeter(const char *, int, int, int, int, int, int, const char *);

void setup()
{
    // get settings from EEPROM
    settings = loadSettings();

    // explicitly start clean
    resLvlRA.clear();
    resRefRA.clear();
    filterRA.clear();

    // switch I2C to alternate pins
    Wire.setSDA(I2C_SDA);
    Wire.setSCL(I2C_SCL);

    pinMode(PUMP_RLY, OUTPUT);
    digitalWrite(PUMP_RLY, LOW);
    pinMode(FLOW_SW, INPUT_PULLUP);
    pinMode(VALVE_RLY, OUTPUT);
    digitalWrite(VALVE_RLY, HIGH);
    pinMode(COMPRESSOR_RLY, OUTPUT);
    digitalWrite(COMPRESSOR_RLY, LOW);
    pinMode(ALARMS_RLY, OUTPUT);
    digitalWrite(ALARMS_RLY, LOW);

    pinMode(TOP_FAN_RPM, INPUT);
    attachInterrupt(TOP_FAN_RPM, top_fan_pulse, FALLING);
    pinMode(BOTTOM_FAN_RPM, INPUT);
    attachInterrupt(BOTTOM_FAN_RPM, bottom_fan_pulse, FALLING);
    topRA.clear();
    bottomRA.clear();
    pinMode(FAN_PWM, OUTPUT);
    analogWriteFrequency(FAN_PWM, 25000);
    readings.chassis.fan.pwm = turnOffFans(FAN_PWM);

    readings.reservoir.setpoint = 20.0;

    SerialUSB.begin(9600);
    while (!SerialUSB && millis() < 5000)
    {
        // wait up to 5 seconds for Arduino Serial Monitor
    }
    SerialUSB.println("RS232 CW_5200 Controller");

    if (!bme.begin(BME_ADDRESS))
    {
        setError(CASE_BME280_NO_CONNECT);
        SerialUSB.printf("Error %04X: No connect to BME!\n", readings.error.code);
    }
    else
    {
        bme_temp->printSensorDetails();
        bme_humidity->printSensorDetails();
    }

    // SSD1306_SWITCHCAPVCC = generate display voltage from 3.3V internally
    if (!display.begin(SSD1306_SWITCHCAPVCC, SCREEN_ADDRESS))
    {
        setError(CASE_DISPLAY_NO_CONNECT);
        SerialUSB.printf("Error %04X: No connect to display!\n", readings.error.code);
    }
    else
    {
        display.setTextSize(1);              // Normal 1:1 pixel scale
        display.setTextColor(SSD1306_WHITE); // Draw white text
        display.setCursor(0, 0);             // Start at top-left corner
        display.cp437(true);                 // Use full 256 char 'Code Page 437' font
    }

    sensors.begin();
    if (!sensors.getAddress(outside_temp, 0))
    {
        setError(CASE_NO_OUTSIDE_DS18B20_ADDRESS);
        SerialUSB.printf("Error %04X: Unable to find address for outside_temp\n", readings.error.code);
    }
    else
    {
        SerialUSB.print("outside_temp Address: ");
        printAddress(outside_temp);
        SerialUSB.println();
        sensors.setResolution(outside_temp, TEMPERATURE_PRECISION);
    }

    if (!sensors.getAddress(reservoir_temp, 1))
    {
        setError(RESERVOIR_NO_DS18B20_ADDRESS);
        SerialUSB.printf("Error %04X: Unable to find address for reservoir_temp\n", readings.error.code);
    }
    else
    {
        SerialUSB.print("reservoir_temp Address: ");
        printAddress(reservoir_temp);
        SerialUSB.println();
        sensors.setResolution(reservoir_temp, TEMPERATURE_PRECISION);
    }

    /*
     *  Set up telemetry link
     */
    Serial1.begin(19200);
    telemetry.begin(Serial1);
    delay(5000);
}

void loop()
{
    handleUSBSerial();
    measureReservoirLevel();
    measureChassisTempHumid();
    measureReservoirTemp();
    measureOutsideTemp();
    measureFanRPM();
    measureFilterDP();
    runCoolingCycle();

    // send telemetry
    txSize = 0;
    txSize = telemetry.txObj(readings, txSize);
    telemetry.sendData(txSize);

    updateDisplay();
    delay(1000); // TODO: REMOVE ME
}

void handleUSBSerial()
{
    if (SerialUSB.available() > 0)
    {
        String command = SerialUSB.readStringUntil('\n');
        char cmd = command.charAt(0);
        char scmd = command.charAt(1);
        SerialUSB.print(command.c_str());
        switch (cmd)
        {
        case 'f':
            /* manual fan control */
            if (scmd == '1')
            {
                readings.chassis.fan.pwm = turnOnFans(FAN_PWM);
                SerialUSB.println("Fans ON");
            }
            else if (scmd == '0')
            {
                readings.chassis.fan.pwm = turnOffFans(FAN_PWM);
                SerialUSB.println("Fans OFF");
            }
            break;

        case 'p':
            /* manual pump control */
            if (scmd == '1')
            {

                digitalWrite(PUMP_RLY, LOW);
                SerialUSB.println("Pump ON");
            }
            else if (scmd == '0')
            {

                digitalWrite(PUMP_RLY, HIGH);
                SerialUSB.println("Pump OFF");
            }
            break;
        case 'r':
            /* reset running averages */
            switch (scmd)
            {
            case 'l': // Levels
                resLvlRA.clear();
                resRefRA.clear();
                SerialUSB.println("Cleared eTape RAs");
                break;
            case 'f': // Filter
                filterRA.clear();
                SerialUSB.println("Cleared filter RAs");
                break;
            case 't': // Tach
                topRA.clear();
                bottomRA.clear();
                SerialUSB.println("Cleared tach RAs");
                break;
            default:
                resLvlRA.clear();
                resRefRA.clear();
                filterRA.clear();
                topRA.clear();
                bottomRA.clear();
                SerialUSB.println("Cleared ALL RAs");
                break;
            }

            break;

        default:
            SerialUSB.println("UNKNOWN COMMAND");
            break;
        }
    }
}

void measureReservoirLevel()
{
    /*
     *   Reservoir Level Measurement
     */
    resLvlRA.addValue(analogRead(RES_LEVEL));
    resRefRA.addValue(analogRead(RES_REF));
    readings.reservoir.level_sense = resLvlRA.getAverage();
    readings.reservoir.level_ref = resRefRA.getAverage();
    if (readings.reservoir.level_sense < settings->reservoir_volume_low_limit)
    {
        setError(RESERVOIR_LEVEL_LOW);
        SerialUSB.printf("Error %04X: Reservoir level too low! %dmL < %dmL\n", readings.error.code, (int)readings.reservoir.level_sense, settings->reservoir_volume_low_limit);
    }
}

void measureChassisTempHumid()
{
    /*
     *   Case Temp and RH Measurement
     */
    sensors_event_t temp_event, humidity_event;
    bme_temp->getEvent(&temp_event);
    bme_humidity->getEvent(&humidity_event);
    readings.chassis.inside_temperature = temp_event.temperature;
    readings.chassis.humidity = humidity_event.relative_humidity;
    if (readings.chassis.inside_temperature > settings->case_temperature_high_limit)
    {
        setError(CASE_TEMP_TOO_HIGH);
        SerialUSB.printf("Error %04X: Case temperature too high! %dC > %dC\n", readings.error.code, readings.chassis.inside_temperature, settings->case_temperature_high_limit);
    }
    if (readings.chassis.inside_temperature < settings->case_temperature_low_limit)
    {
        setError(CASE_TEMP_TOO_LOW);
        SerialUSB.printf("Error %04X: Case temperature too low! %dC < %dC\n", readings.error.code, readings.chassis.inside_temperature, settings->case_temperature_low_limit);
    }
    if (readings.chassis.humidity > settings->case_humidity_high_limit)
    {
        setError(CASE_HUMIDITY_TOO_HIGH);
        SerialUSB.printf("Error %04X: Case humidity too high! %d%% > %d%%\n", readings.error.code, readings.chassis.humidity, settings->case_humidity_high_limit);
    }
}

void measureReservoirTemp()
{
    /*
     *   Reservoir Temp Measurement
     */
    sensors.requestTemperaturesByAddress(reservoir_temp);
    readings.reservoir.temperature = sensors.getTempC(reservoir_temp);
    if (readings.reservoir.temperature == DEVICE_DISCONNECTED_C)
    {
        setError(RESERVOIR_NO_DS18B20_READ);
        SerialUSB.printf("Error %04X: Could not read reservoir temperature data\n", readings.error.code);
        readings.reservoir.temperature = 0.0;
    }
    if (readings.reservoir.temperature > settings->reservoir_temp_high_limit)
    {
        setError(RESERVOIR_TEMP_TOO_HIGH);
        SerialUSB.printf("Error %04X: Reservoir temperature too high! %dC > %dC\n", readings.error.code, readings.reservoir.temperature, settings->reservoir_temp_high_limit);
    }
    if (readings.reservoir.temperature < settings->reservoir_temp_low_limit)
    {
        setError(RESERVOIR_TEMP_TOO_LOW);
        SerialUSB.printf("Error %04X: Reservoir temperature too low! %dC < %dC\n", readings.error.code, readings.reservoir.temperature, settings->reservoir_temp_low_limit);
    }
}

void measureOutsideTemp()
{
    /*
     *   Outside Temp Measurement
     */
    sensors.requestTemperaturesByAddress(outside_temp);
    readings.chassis.outside_temperature = sensors.getTempC(outside_temp);
    if (readings.chassis.outside_temperature == DEVICE_DISCONNECTED_C)
    {
        setError(CASE_NO_OUTSIDE_DS18B20_READ);
        SerialUSB.printf("Error %04X: Could not read outside temperature data\n", readings.error.code);
        readings.chassis.outside_temperature = 0.0;
    }
    if (readings.chassis.outside_temperature > settings->outside_temp_high_limit)
    {
        setError(CASE_OUTSIDE_TEMP_TOO_HIGH);
        SerialUSB.printf("Error %04X: Outside temperature too high! %dC > %dC\n", readings.error.code, readings.chassis.outside_temperature, settings->outside_temp_high_limit);
    }
    if (readings.chassis.outside_temperature < settings->outside_temp_low_limit)
    {
        setError(CASE_OUTSIDE_TEMP_TOO_LOW);
        SerialUSB.printf("Error %04X: Outside temperature too low! %dC < %dC\n", readings.error.code, readings.chassis.outside_temperature, settings->outside_temp_low_limit);
    }
}

void measureFilterDP()
{
    /*
     *   Filter Delta-P Measurement
     */
    filterRA.addValue(analogRead(FILTER_P));
    readings.chassis.filter_dp = filterRA.getAverage();
    if (filterRA.getAverage() > settings->filter_high_limit)
    {
        setError(CASE_FILTERS_CLOGGED);
        SerialUSB.printf("Error %04X: Filter delta-P too high! %d > %d\n", readings.error.code, (int)readings.chassis.filter_dp, settings->filter_high_limit);
    }
}

void measureFanRPM()
{
    /*
     *   Fan RPM Measurement
     */
    if (top_fan.ready)
    {
        topRA.addValue(top_fan.pulse_len);
        top_fan.ready = false;
    }
    if (bottom_fan.ready)
    {
        bottomRA.addValue(bottom_fan.pulse_len);
        bottom_fan.ready = false;
    }
    if (millis() - reading_time > FAN_SAMPLING_TIME)
    {
        if (topRA.getCount() > 0)
        {
            readings.chassis.fan.top_tach = convertMicrosToRPM(topRA.getAverage());
        }
        else
        {
            readings.chassis.fan.top_tach = 0;
            if (readings.chassis.fan.pwm > 0)
            {
                setError(CASE_TOP_FAN_LOW_RPM);
                SerialUSB.printf("Error %04X: Top fan RPM too low!\n", readings.error.code);
            }
        }

        if (bottomRA.getCount() > 0)
        {
            readings.chassis.fan.bottom_tach = convertMicrosToRPM(bottomRA.getAverage());
        }
        else
        {
            readings.chassis.fan.bottom_tach = 0;
            if (readings.chassis.fan.pwm > 0)
            {
                setError(CASE_BOTTOM_FAN_LOW_RPM);
                SerialUSB.printf("Error %04X: Bottom fan RPM too low!\n", readings.error.code);
            }
        }
    }
}

void runCoolingCycle()
{
    /*
     *   Cooling Cycle
     */
    readings.compressor.compressor_time = millis() - last_compressor;
    readings.compressor.valve_time = millis() - last_valve;
    readings.pump.flow_ok = (digitalRead(FLOW_SW) == LOW);
    readings.pump.running = (digitalRead(PUMP_RLY) == LOW);

    if (running_state)
    {
        if (readings.reservoir.temperature > readings.reservoir.setpoint + settings->hysteresis)
        {
            if (digitalRead(VALVE_RLY) == HIGH)
            {
                last_valve = millis();
                digitalWrite(VALVE_RLY, LOW);
                readings.compressor.valve = true;
            }
            if (readings.compressor.valve_time >= settings->valve_lockout && readings.compressor.compressor_time >= settings->compressor_lockout)
            {
                last_compressor = millis();
                readings.chassis.fan.pwm = turnOnFans(FAN_PWM);
                digitalWrite(COMPRESSOR_RLY, HIGH);
                readings.compressor.running = true;
            }
        }
        if (readings.reservoir.temperature <= readings.reservoir.setpoint - settings->hysteresis)
        {
            if (millis() - last_compressor >= settings->compressor_lockout)
            {
                last_compressor = millis();
                last_valve = millis();
                readings.chassis.fan.pwm = turnOffFans(FAN_PWM);
                topRA.clear();
                bottomRA.clear();
                digitalWrite(COMPRESSOR_RLY, LOW);
                digitalWrite(VALVE_RLY, HIGH);
                readings.compressor.running = false;
                readings.compressor.valve = false;
            }
        }
        if (readings.pump.running && !readings.pump.flow_ok)
        {
            setError(RESERVOIR_PUMP_ON_WITH_NO_FLOW);
            SerialUSB.printf("Error %04X: No flow with pump running!\n", readings.error.code);
        }
    }
}

void setError(uint16_t error)
{
    readings.error.code = error;
    readings.error.alert = true;
    digitalWrite(ALARMS_RLY, LOW);
}

// function to print a device address
void printAddress(DeviceAddress deviceAddress)
{
    for (uint8_t i = 0; i < 8; i++)
    {
        // zero pad the address if necessary
        if (deviceAddress[i] < 16)
            SerialUSB.print("0");
        SerialUSB.print(deviceAddress[i], HEX);
    }
}

void updateDisplay()
{
    /*
     *   Display Update Cycle
     */
    if (millis() - reading_time >= PAGE_DELAY)
    {
        reading_time = millis();
        ++reading_state;
        if (reading_state >= 6)
            reading_state = 0;
        switch (reading_state)
        {
        case 0:
            display.clearDisplay();
            ringMeter("Case T", readings.chassis.inside_temperature, 0, 100, 0, 0, GAUGE_RADIUS, "\xF8"
                                                                                                 "C");
            ringMeter("Case RH", readings.chassis.humidity, 0, 100, SCREEN_WIDTH - 2 * GAUGE_RADIUS, 0, GAUGE_RADIUS, "%");
            display.display();
            break;
        case 1:
            display.clearDisplay();
            ringMeter("Res T", readings.reservoir.temperature, 0, 100, 0, 0, GAUGE_RADIUS, "\xF8"
                                                                                           "C");
            ringMeter("Out T", readings.chassis.outside_temperature, 0, 100, SCREEN_WIDTH - 2 * GAUGE_RADIUS, 0, GAUGE_RADIUS, "\xF8"
                                                                                                                               "C");
            display.display();
            break;
        case 2:
            display.clearDisplay();
            ringMeter("Top Fan", readings.chassis.fan.top_tach, 0, 6000, 0, 0, GAUGE_RADIUS, "RPM");
            ringMeter("Bot Fan", readings.chassis.fan.bottom_tach, 0, 6000, SCREEN_WIDTH - 2 * GAUGE_RADIUS, 0, GAUGE_RADIUS, "RPM");
            display.display();
            break;
        case 3:
            display.clearDisplay();
            ringMeter("Res Lvl", (int)readings.reservoir.level_sense, 0, 1024, 0, 0, GAUGE_RADIUS, "ADC");
            ringMeter("Res Ref", (int)readings.reservoir.level_ref, 0, 1024, SCREEN_WIDTH - 2 * GAUGE_RADIUS, 0, GAUGE_RADIUS, "ADC");
            display.display();
            break;
        case 4:
            display.clearDisplay();
            ringMeter("Res Set", readings.reservoir.setpoint, 10, 30, 0, 0, GAUGE_RADIUS, "\xF8"
                                                                                          "C");
            ringMeter("\x83 P", (int)readings.chassis.filter_dp, 0, 1024, SCREEN_WIDTH - 2 * GAUGE_RADIUS, 0, GAUGE_RADIUS, "ADC");
            display.display();
            break;
        case 5:
            display.clearDisplay();
            ringMeter("Comp", readings.compressor.compressor_time / 1000, 0, (2 * settings->compressor_lockout) / 1000, 0, 0, GAUGE_RADIUS, "s");
            ringMeter("Valve", readings.compressor.valve_time / 1000, 0, (2 * settings->valve_lockout) / 1000, SCREEN_WIDTH - 2 * GAUGE_RADIUS, 0, GAUGE_RADIUS, "s");
            display.display();
            break;
        default:
            break;
        }
    }
}

void top_fan_pulse()
{
    top_fan.current_pulse = micros();
    top_fan.pulse_len = top_fan.current_pulse - top_fan.last_pulse;
    top_fan.last_pulse = top_fan.current_pulse;
    top_fan.ready = true;
}

void bottom_fan_pulse()
{
    bottom_fan.current_pulse = micros();
    bottom_fan.pulse_len = bottom_fan.current_pulse - bottom_fan.last_pulse;
    bottom_fan.last_pulse = bottom_fan.current_pulse;
    bottom_fan.ready = true;
}
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

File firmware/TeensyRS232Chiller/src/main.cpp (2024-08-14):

#include <Arduino.h>
#include <RunningAverage.h>
#include <OneWire.h>
#include <DallasTemperature.h>

#define ONE_WIRE 2   // DS18B20 bus
#define RES_LEVEL A9 // Analog input for eTape Rsense
#define RES_REF A8   // Analog input for eTape Rref

RunningAverage resLvlRA(100);
RunningAverage resRefRA(100);

#define TEMPERATURE_PRECISION 9
OneWire oneWire(ONE_WIRE);
DallasTemperature sensors(&oneWire);
DeviceAddress outside_temp = {0x28, 0x4E, 0x6A, 0x45, 0x92, 0x17, 0x02, 0xEC};
DeviceAddress reservoir_temp = {0x28, 0xFF, 0x02, 0x5D, 0xC1, 0x17, 0x05, 0xCB};
float reservoir_temp_reading = 0.0;
float outside_temp_reading = 0.0;

char msg;
bool pause;
uint32_t timeout = 0;
uint8_t samples = 0;
uint8_t retries = 0;

void setup(void)
{
  Serial.begin(9600);
  while (!Serial && millis() < 5000)
  {
    // wait up to 5 seconds for Arduino Serial Monitor
  }
  Serial.println("Chiller-side RS-232 Test");

  // explicitly start clean
  resLvlRA.clear();
  resRefRA.clear();

  sensors.begin();
  if (!sensors.getAddress(outside_temp, 0))
  {
    Serial.println("Error: Unable to find address for outside_temp");
  }
  else
  {
    sensors.setResolution(outside_temp, TEMPERATURE_PRECISION);
  }

  if (!sensors.getAddress(reservoir_temp, 1))
  {
    Serial.println("Error: Unable to find address for reservoir_temp");
  }
  else
  {
    sensors.setResolution(reservoir_temp, TEMPERATURE_PRECISION);
  }
  pause = true;
}

void loop()
{
  if (!pause)
  { /*
     *   Reservoir Temp Measurement
     */
    sensors.requestTemperatures();
    reservoir_temp_reading = sensors.getTempC(reservoir_temp);
    if (reservoir_temp_reading == DEVICE_DISCONNECTED_C)
    {
      retries = 0;
      while (++retries <= 3)
      {
        sensors.requestTemperaturesByAddress(reservoir_temp);
        reservoir_temp_reading = sensors.getTempC(reservoir_temp);
        if (reservoir_temp_reading == DEVICE_DISCONNECTED_C)
        {
          break;
        }
      }
      if (retries >= 3)
      {
        Serial.println("Error: Could not read reservoir temperature data");
        reservoir_temp_reading = 0.0;
      }
    }
    else
    {
      retries = 0;
    }

    /*
     *   Outside Temp Measurement
     */
    outside_temp_reading = sensors.getTempC(outside_temp);
    if (outside_temp_reading == DEVICE_DISCONNECTED_C)
    {
      retries = 0;
      while (++retries <= 3)
      {
        sensors.requestTemperaturesByAddress(outside_temp);
        outside_temp_reading = sensors.getTempC(outside_temp);
        if (outside_temp_reading == DEVICE_DISCONNECTED_C)
        {
          break;
        }
      }
      if (retries >= 3)
      {
        Serial.println("Error: Could not read outside temperature data");
        outside_temp_reading = 0.0;
      }
    }
    else
    {
      retries = 0;
    }
    if (millis() - timeout >= 10)
    {
      timeout = millis();
      resLvlRA.addValue(analogRead(RES_LEVEL));
      resRefRA.addValue(analogRead(RES_REF));
      ++samples;
    }
    if (samples >= 100)
    {
      Serial.printf("%.2f,%.2f,%.2f,%.2f,%.2f,%.2f\n",
                    resLvlRA.getAverage(),
                    resLvlRA.getStandardDeviation(),
                    resRefRA.getAverage(),
                    resRefRA.getStandardDeviation(),
                    outside_temp_reading,
                    reservoir_temp_reading);
      samples = 0;
    }
  }

  if (Serial.available() > 0)
  {
    msg = Serial.read();
    if (msg == 'r')
    {
      Serial.println("Reset!");
      resLvlRA.clear();
      resRefRA.clear();
      timeout = 0;
      samples = 0;
    }
    if (msg == 'p')
    {
      Serial.println("Pause!");
      pause = true;
    }
    if (msg == 's')
    {
      Serial.println("Start!");
      pause = false;
    }
  }
}

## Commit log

2024-05-10 Converted to KiCad 8.0
    [can_pcie_water_loop.kicad_pcb, can_pcie_water_loop.kicad_sch]
2024-05-10 Further converted to KiCad 8.0
2024-05-10 Replaced CAN transciever with MAX3232
    [can_pcie_water_loop.kicad_sch]
2024-05-10 Hopefully image rendering from https://github.com/linalinn/kicad-render?tab=readme-ov-file
    [pcie_water_loop_controller.csv, pcie_water_loop_controller.kicad_pcb, pcie_water_loop_controller.kicad_sch]
2024-08-01 Changed PCIe card from CAN to RS232 via MAX3232
    [pcie_water_loop_controller.kicad_pcb, pcie_water_loop_controller.kicad_sch]
2024-08-01 Minor board fixes, updated PCIe README
    [pcie_water_loop_controller.kicad_pcb, pcie_water_loop_controller.kicad_sch]
2024-08-01 Moved to subdir
    [pcie_water_loop_controller.csv, pcie_water_loop_controller.kicad_pcb, pcie_water_loop_controller.kicad_sch]
2024-08-02 Initial progress on CW-5200 local control board.
    [cw-5200_controller.kicad_pcb, cw-5200_controller.kicad_sch]
2024-08-02 Repinning to ease routing.
    [cw-5200_controller.kicad_sch]
2024-08-02 ignore KiCAD lockfiles
2024-08-02 Corrected for OLED pinout.
    [pcie_water_loop_controller.kicad_pcb, pcie_water_loop_controller.kicad_sch]
2024-08-02 Finalized routing.
    [cw-5200_controller.kicad_pcb]
2024-08-02 fixed silk for OLED pinout
    [pcie_water_loop_controller.kicad_pcb]
2024-08-13 Assembly BOMs.
    [cw-5200_controller.kicad_pcb]
2024-08-14 testing eTape calibration
    [eTape_Processed.csv, eTape_Readings.csv]
2024-08-18 Added zero points for sensor calibrations
2024-08-18 Broke out to functions per measurement
    [main.cpp]
2024-08-18 Added fan-specific files, retooled RPM measurement.
2024-08-18 Made fan control more explicit, clear RPM averages when fans off.
2024-08-19 Maybe pcb images fixed?
2024-08-19 Copy over KiCAD iboms to somewhere linkable
2024-08-19 Doing the fan tach the hard way because i missed the pin limitations of FreqMeasureMulti on the board...
2024-09-17 I2CDriver testing of ABP2 sensor
